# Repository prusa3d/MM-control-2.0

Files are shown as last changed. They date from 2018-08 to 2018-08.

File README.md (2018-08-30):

# PRUSA MM control board

KiCad PCB layout
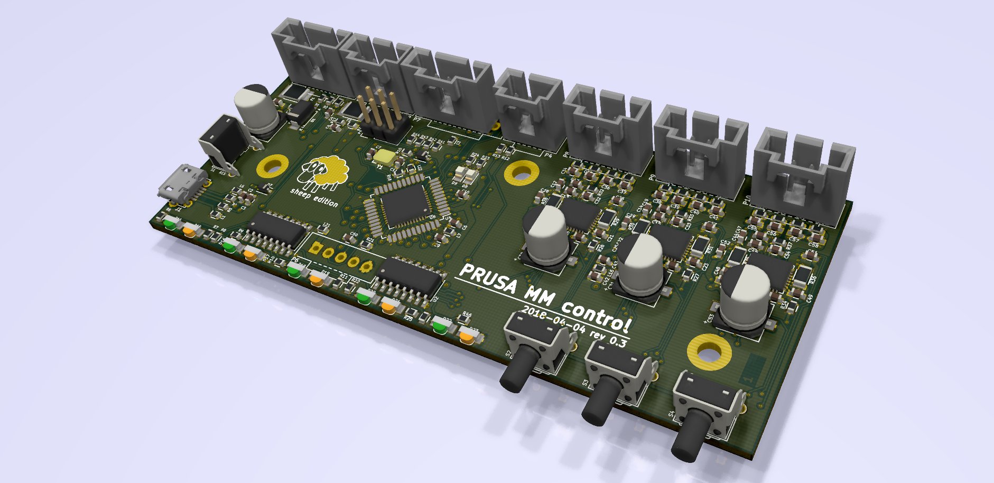
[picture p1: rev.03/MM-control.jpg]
PCB


* [Interactive bom](http://htmlpreview.github.io/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)
* [STEP 3D model](rev.03/MM-control.step)
* [Firmware](https://github.com/prusa3d/MM-control-01)

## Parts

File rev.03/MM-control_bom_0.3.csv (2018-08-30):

Component | Description | Part | References | Value | Footprint | Quantity Per PCB | Req
1 | Unpolarized capacitor | C | C1 C2 C4 C9 C12 C14 C16 C17 C18 C19 C20 C21 C22 C23 C24 C25 C26 C27 C28 C29 C42 C44 C46 C47 C48 C49 C50 C51 C52 C60 | 100n | C_0603 | 30 | 50V/X7R/10%
2 |  | Csmall | C8 | 100n | C_0603 | 1 | 50V/X7R/10%
3 | Polarised capacitor | CP_Small | C30 C31 C53 C59 | 100u | c_elec_6.3x7.7 | 4 | 35V/20%
4 | Unpolarized capacitor | C | C3 | 10u | C_0603 | 1 | 6,3V/X5R/20%
5 | Polarised capacitor | CP_Small | C43 | 10u | C_0603 | 1 | 6,3V/X5R/20%
6 | Unpolarized capacitor | C_Small | C34 C35 C36 C37 C38 C39 C40 C41 C55 C56 C57 C58 | 1n | C_0603 | 12 | 50V/X7R/10%
7 | Unpolarized capacitor | C | C6 C10 C32 C33 C54 | 1u | C_0603 | 5 | 6,3V/X5R/10%
8 | Unpolarized capacitor | C_Small | C13 C15 C45 | 22n | C_0603 | 3 | 50V/X7R/10%
9 |  | Csmall | C7 C11 | 22p | C_0603 | 2 | 50V/C0G/10%
10 | Diode, alternativ symbol | D_ALT | D6 D7 | BAS16HT1G | SOD-323 | 2
11 | LED, small symbol, alternativ symbol | LED_Small_ALT | D14 D16 D18 D20 D22 | KPA-3010MGC | LED-1104 | 5
12 | LED, small symbol, alternativ symbol | LED_Small_ALT | D15 D17 D19 D21 D23 | KPA-3010SECK | LED-1104 | 5
13 | LED generic, alternativ symbol | LED_ALT | D8 | RX | LED_0805 | 1
14 | Diode, alternativ symbol | D_ALT | D1 | SK310SMA-DIO | SMA_Standard | 1
15 | LED generic, alternativ symbol | LED_ALT | D9 | TX | LED_0805 | 1
16 | resettable fuse, polymeric positive temperature coefficient (PPTC), small symbol | Polyfuse_Small | F1 | 150mA | R_1812 | 1
17 | resettable fuse, polymeric positive temperature coefficient (PPTC), small symbol | Polyfuse_Small | F2 | 750mA | R_1812 | 1
18 |  | USB-micro | J1 | MX-105017-0001 | USB-micro | 1
19 | Inductor with ferrite core, small symbol | L_Core_Ferrite_Small | L1 L2 L3 L5 L6 L7 L8 L9 L10 L11 L12 L13 L14 L15 L16 L17 L18 L19 L20 L21 L22 | FB BLM18KG121TN1D | R_0603 | 21
20 |  | CONN_3X2 | P5 | ICSP | Pin_Header_Straight_2x03 | 1
21 | Connector, single row, 01x03 | CONN_01X03 | P4 | MOLEX 70543-0002 | Pin_1x03-XL | 1
22 | Connector, single row, 01x04 | CONN_01X04 | P8 P9 P10 | MOLEX 70543-0003 | Pin_1x04-XL | 3
23 | Connector, double row, 02x02 | CONN_02X02 | P2 | MOLEX 70543-0003 | Pin_1x04-XL | 1
24 | Connector, single row, 01x06 | CONN_01X06 | P7 | MOLEX 70543-0004 | Pin_1x06-XL | 1
25 | Connector, single row, 01x05 | CONN_01X05 | P1 | MOLEX 70543-0004 | Pin_1x05-XL | 1
26 | Connector, single row, 01x05 | CONN_01X05 | P6 | ShiftOut | Pin_1x05-XL | 1
27 | Resistor | R | R41 R42 R43 R44 | 0R | R_0603 | 4 | 0,1W/5%
28 | Resistor | R | R12 | 100R | R_0603 | 1 | 0,1W/1%
29 | Resistor | R | R32 R33 R37 | 10R | R_0603 | 3 | 0,1W/1%
30 | Resistor | R | R13 R15 R16 R21 R26 R27 R34 | 10k | R_0603 | 7 | 0,1W/1%
31 | Resistor | R | R38 | 15k | R_0603 | 1 | 0,1W/1%
32 | Resistor | R | R18 | 1M | R_0603 | 1 | 0,1W/1%
33 | Resistor | R | R17 R23 R24 | 1k | R_0603 | 3 | 0,1W/1%
34 | Resistor | R | R39 R40 | 1k5 | R_0603 | 2 | 0,1W/1%
35 | Resistor | R | R1 R2 R4 R5 | 22R | R_0603 | 4 | 0,1W/1%
36 | Resistor | R | R6 R7 R8 R9 R10 R11 R22 R25 R45 R46 | 330R | R_0603 | 10 | 0,1W/1%
37 | Resistor | R | R28 R29 R30 R31 R35 R36 | R22 | R_1206 | 6 | 0,5W/1%
38 |  | TACT-SW2 | S4 | DWN | TACT-90 | 1
39 |  | TACT-SW2 | S2 | OK | TACT-90 | 1
40 |  | TACT-SW2 | S1 | RES | TACT-90 | 1
41 |  | TACT-SW2 | S3 | UP | TACT-90 | 1
42 |  | 74HC595 | U2 U9 | 74HC595 | SOIC-16_3.9x9.9mm_Pitch1.27mm | 2
43 |  | ATmega32U4 | U4 | ATmega32U4 | TQFP-44_10x10mm_Pitch0.8mm | 1
44 |  | ATmega32U4 | U8 | ATmega32U4 | QFN-44-1EP_7x7mm_Pitch0.5mm | 1
45 |  | TCM2130-LA | U5 U6 U7 | TMC2130-LA | QFN-36-1EP_5x6mm_Pitch0.5mm-GNDpad-0.3mm | 3
46 | Four pin crystal (GND on pins 2 and 4), e.g. in SMD package | Crystal_GND24 | Y1 | LFXTAL035264BULK 16MHz | Crystal-3.2x2.5mm | 1
Component Groups: | 46
Component Count: | 161
Fitted Components: | 161
Number of PCBs: | 1
Total components: | 161
Schematic Version: | 0.3

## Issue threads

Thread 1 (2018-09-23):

kiCAD files do not reflect actual MMU2 production board.

CacikeOtoao, 2018-09-23:
@ok1hra Production boards of the MMU2 that people are getting are showing re work to the vias (to the upper right of the sheep logo) after manufacturing that are not reflected on the Source files provided here. Keep in mind that these files were made public after the MMU2 was released and corrections as described above had been made to the boards. Please provide updated documentation or comments regarding these changes as good Open Source practice. Providing outdated information to the community is not a good practice since the community depends on these files to replicate the boards and Prusa Research preaches about Open Source.

ericclinedinst, 2018-09-23:
My level of surprise is absolutely zero.

ok1hra, 2018-09-23:
@CacikeOtoao thanks for comment. Can you show me this difference? Because revision 0.3 is last production version

ericclinedinst, 2018-09-23:
@ok1hra  for starters R42, d7, r44 are removed on the boards you're shipping.   Where as the BOM has them in place.

ericclinedinst, 2018-09-23:
In some photos it appears that traces have been cut above the sheep on the right side just above his butt.

Also when will we be getting the bootloader that was spoken about in anot her github thead? You guys said a week ago it would be posted in "days" @ok1hra

ok1hra, 2018-09-23:
And you can post this photos? Without another argument you claim is false.

I am not manage bootloader, I cant help you. Ask on support desk.

Closed 2018-09-23.

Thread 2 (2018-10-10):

The orentation of the sockets should be turned by 180°

KarlZeilhofer, 2018-10-10:
Is there any chance, that the sockets will be turned by 180°?
With the current case of the MMU 2.0 is nearly impossible to unplug the cables when everything is assembled.

ok1hra, 2018-10-11:
We do not have the same feeling.

KarlZeilhofer, 2018-10-18:
No, why not? I think to remember, that the trouble shooting guide says to use an allen key to unlock the securing pin of the communication plug.

domesticatedviking, 2019-09-16:
I very much agree.  When using an enclosure, all of the connections to the MMU2 are in a location that can neither be seen nor reached from the front of the printer, and they all require tools to remove.   The result is that it is VERY difficult to remove the printer for maintenance.   This is why I designed the [underslung control panel mod](https://www.thingiverse.com/thing:3211711).

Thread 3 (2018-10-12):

100nF for VCC of MCU

KarlZeilhofer, 2018-10-12:
I would suggest 100nF ceramic capacitor for pins 2, 14 and 34, since they are all powered via ferrite beads, just to be on the save side.

ok1hra, 2018-10-17:
Yes, good idea for next version. Thanks.

pacaj2am, 2021-02-14:
wow... having issues with my board... looking into the design... haven't expected such a design flaws (as well as the C60 issue
https://github.com/prusa3d/MM-control-2.0/issues/12)

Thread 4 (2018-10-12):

Signal directions of global labels should be corrected

KarlZeilhofer, 2018-10-12:
Many labels are pointing into the wrong directions.

This is more a matter of taste: Since KiCad has no ability to automatically show where global labels are referenced, I would prefer wires instead of excessive usage of labels, where easily possible:
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

ok1hra, 2018-10-17:
Does not affect to functionality :)

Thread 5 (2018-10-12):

ERC Errors should be cleaned up

KarlZeilhofer, 2018-10-12:
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

The use of the power-flag should fix many of them. We at Team14 also use passives with a dedicated direction, to give the ERC more chances to detect errors.
Once I wrote an article about that: http://www.zeilhofer.co.at/wiki/doku.php?id=resistors_and_void-pointers

Many of them would need to modify the MCU symbol pins to outputs, which isn't very handy either. That's a common problem. Perhaps one could introduce a special symbol, similar to a power-flag, which declares a driver to that net (virtual symbol with a single "output" pin).

ok1hra, 2018-10-17:
Nice tutorial, thanks.

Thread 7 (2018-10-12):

TODO: button expansion connector

KarlZeilhofer, 2018-10-12:
just a duplicate of a note in the schematic :)

ok1hra, 2018-10-17:
also in plan

Wheart, 2021-11-27:
Is it implemented on 0.4.4?

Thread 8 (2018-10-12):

Missing comments about number of axis and LEDs

KarlZeilhofer, 2018-10-12:
I know, this is defined in software, but it helps, if it is clearly visible in the schematics too.

ok1hra, 2018-10-17:
yes, but is not exact :)

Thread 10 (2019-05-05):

noise in idle, homing problems, led flickering

SNDR0, 2019-05-05:
like said from @chriswal, adding  a ceramic capacitor 104 between pin 16 and ground of every 74hc595 you solve the problem. (issue known when you are using 74hc595)

darBis, 2019-06-13:
I had recently solved these issues by adding 100 nF capacitors to 74hc595 ICs also.(https://github.com/prusa3d/MM-control-01/issues/124#issuecomment-501355623)
Please add bypass capacitors to those ICs in next revision of the board.
Information about this issue and working solution is relatively hard to find, maybe some list of known issues on wiki would be great.

darBis, 2019-08-24:
This is a serious reliability issue. Since fixing my board by adding those caps i have no more issues with the MMU regarding homing errors and erratic behaviour.

chriswal, 2019-08-24:
i also made a firmware workaround for people who cant modify the board on there own. there is a pull request. or you can get it from my fork

bbeller123, 2020-07-30:
Prusa should add a screen with graphic interface for multi material. I mean it's multi color ?

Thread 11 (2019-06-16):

mmu2 stepper are always powered up

sylphio, 2019-06-16:
hi,
   my prusa mk3 use octoprint on a internal raspberry, so i leave the printer always on.
Just realised that after 2 day of idling the mmu2 steeper are still hot and powered. (the printer steeper are cold)
It is not great for power consumtion and for long term usage.

Is it possible to powerdown after a certain time of inactivity?

Thank you

sylphio, 2019-06-16:
Just realized this one is for the hardware and not the sorftware

Closed 2019-06-16.

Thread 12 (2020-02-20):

C60 can cause timing issues

NielschB, 2020-02-20:
I have experienced some issues with my MMU2 board, where all LEDs started flashing and could not get the motors working anymore. All pinned down to capacitor C60 which is connected to the latch input of the shift registers. This caused a slow ramp of the latch signal which resulted in timing issues on the shiftregister side. After reviewing the schematics I wonder why C60 is there in the first place. If its function is to implement a low-pass filter, then a series resistor should be added, now its determined by the Atmega output drive strength.
All together this is not a nice way to do this since a slow signal ramp is applied to a digital input (cross currents etc.) Another thing is that continuously charging and discharging this cap by the MCU is a waste of current.

chriswal, 2020-07-30:
and you resolved this issue by removing C60?

NielschB, 2020-07-30:
Yes, just remove it

NielschB, 2020-07-30:
This C60 might just be there to give non-prusa sellers a hard time ;) I have the feeling that the original Prusa boards might not have this cap assembled.

chriswal, 2020-07-30:
You are right , there should be a resistor in series. but i dont see where there is a timining issue. the enable signals are always on, only the dir signals can change because of the direction the motor is moving. the leds are working also without a problem.
so what is the timing issue you are refering about?

NielschB, 2020-07-30:
Most boards don't show the issue, I have had 2 boards that did have this timing issue. Most probably its related to the output drive strength of the MCU where the cap is connect to, which determines the slope of the latch signal. It might vary over batches. Again, in the end a design should never have an analog LPF on a digital input like this.

When the MCU is shifting out data to the shift registers, the latch signal should toggle at a certain moment in time to load the data in the registers. When the latch signal is being delayed (By the cap and finite drive strength of MCU) the latch signal is crossing the shift register's threshold when next data is already shifted in! which causes corruption of the data in the shift registers.

chriswal, 2020-07-30:
So you had flickering leds and loud motor noises on this boards?

NielschB, 2020-07-30:
Flickering leds yes, motors would just not turn in my case, but I expect anything can hapen.
May I ask why you are interested? Are you experiencing the same issues?

chriswal, 2020-07-30:
i edited the message before.  yes i had this issue and solved it a different way.

chriswal, 2020-07-30:
if the motor doesnt turn then this could be some different problem than mine

NielschB, 2020-07-30:
I did try the buffer capacitors, did not help for me. Then I traced it down to this issue which was confirmed with scope measurements.
I am wondering if the people who fix their issue with adding decoupling caps to the shift registers are actually suffering this C60 issue and the error is masked with adding buffer caps. Charging / discharging C60 takes quite some current which could explain why adding buffer caps could help.

Shift registers producing random data due to lack of decoupling caps would mean that the supply drops significantly, which I personally have not observed. (I did measure it actually)

chriswal, 2020-07-30:
but that is a small capacitor and it is charged from the mcu... so for the layout that is further away from the register.
i think to measure this you have to have a very fast scope. is it possible that on these board you had wrong capacitors assembled?
i caan repoduce it on my board if i remove the buffer capacitors.. i also made a workaround in the firmware where you dont change leds while moving the motor ..
i can try to remove the capacitor..i think they added it because they had problems before with erratic output

chriswal, 2020-07-30:
i didnt build this system ..i had this board ..and some of the people are not able to solder.. so i made this workaround ..
i can solder so i can fix something..i have a 100mhz scope but not around at the moment. and this was not an assumption
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
from the datashhet

chriswal, 2020-07-30:
but there can be multiple problems leading to the same outcome. thats why i am interested to find the real problem.
there is also a problem with the design of the 5v power on this board.

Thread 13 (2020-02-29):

Cables

ThomasLGauthier, 2020-02-29:
Hello everyone,

I'd like to implement https://www.prusaprinters.org/prints/7499-prusa-mmu2-moving-filament-passage-22mm-ikea-plats, but the cables between the MMU2S and the MK3S are too short. What cables do I need to buy in a longer form to do what I want? What are the names/links to them? I am also planning to move the power unit outside the enclosure, so what cables might I need to get for that?

Sincerely,
Thomas Gauthier

covertpluto3502, 2022-12-29:
They're molex SL connectors, more specifically the 2.54mm pitch single row versions

Grab some long dupont breadboard jumper wires and take the plastic housings off.

Buy these:(4 pin male, 4 pin female, 5 pin male, 5 pin female)

https://uk.rs-online.com/web/p/wire-housings-plugs/6795971
https://uk.rs-online.com/web/p/wire-housings-plugs/9081005

https://uk.rs-online.com/web/p/wire-housings-plugs/6783161
https://uk.rs-online.com/web/p/wire-housings-plugs/6795921

Then just jam the metal ends of the dupont wires into the housings so the pins on both ends match up. The female ends on the dupont wires(the one with a hole on its end) goes into the female housing and vice versa

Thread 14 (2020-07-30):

Feature Request: Add LCD and Pass Selftest for Multi-Material Upgrade

bbeller123, 2020-07-30:
Prusa should add a screen for the multi material. It would help solve and/or explain problems through graphic text to the user. Something with the color display like the Prusa Mini?

With the screen, there could be a pass selftest feature similar to the current MK3S.

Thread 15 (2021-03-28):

Design error on +5V net

HenrikBork, 2021-03-28:
Hi,
There seems to be a bug in the design regarding the +5V net.
On my MMU2 i measured 4.2V on the +5V, which is too little for the MCU to run 16MHz. This is seemed to be the reason why my MMU was almost unusable as the MCU resets all the time.
Connecting the usb to a host helped a little on stabillity (and the +5V voltage rose 50-100mV)
I have shorted D1 on the MMU PCB, as a "proof-of-problem", and that raised the voltage to 4.8V and removed all MMU misbehavings. (without the usb connected). In the same bug chasing i also added 1000uF between the shorted D1 and GND. I think C59 was probably just fine as it is. (i was tiered of bug chasing the MMU)
**Please note: this is not a proposal to a solution, just "proof" of some kind of an issue with the +5V (at least on my MMU). I have no understanding of the diode's function in the entire printers power nets.** -although this hack has been working for some time now.

So it seems as if the designer was aiming for generating +5V by means of the TMC2130. But forgot to connect the VSA to >6V. But then again why differ so much from the suggested circuit and component values?...
The solution of using the printers +5V through a diode and a inductor yields too low a voltage.
...so it seems as the +5V was forgotten, but it somehow sometimes almost works...

My hope is that Prusa fix this problem in the hardware design. (and sends me a fixed PCB free of charge ;-)

### You're welcome,
### Henrik B. S.

My setup:
Original Prusa I3MK3 (2-3 years old), since then upgraded with factory parts.
MMU2 bought from Prusa around august 2020.
MMU PCB reads "2019-09 rev 0.4.4"
My ugly hack:
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

extra info:
I also reported/discussed this on [https://forum.prusaprinters.org/forum/original-prusa-i3-mmu2s-mmu2-hardware-firmware-and-software-help/i-found-serious-design-error-in-mmu2-electronics-hardware/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](https://forum.prusaprinters.org/forum/original-prusa-i3-mmu2s-mmu2-hardware-firmware-and-software-help/i-found-serious-design-error-in-mmu2-electronics-hardware/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)
...My daytime job is to do this kind of work as consultant - so next time just hire me :-)

Chrismettal, 2021-05-22:
Can confirm, my board started to reset every time it needed to unload filament, getting stuck and requiring user input on every single filament change.
Bypassing the diode raised the 5 V rail from 4.6 V to 4.95 V in idle, fixing the resetting issue for now. Before I could see dips under 4.5 V on the rail on filament changes at which point the MCU sometimes reset.

The capacitor does not seem to be required for me, but I have also added the missing decoupling caps on the shift registers.

Thank you for your find and I sincerely hope Prusa did not abandon the MMU2 and are going to release a new Version of the board (Or maybe at least publish the sources of the most recent version since this repo is behind the actually released boards)

ANTALIFE, 2022-01-03:
Good catch! Looks like quite a big HW bug...
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

ChrisPetit, 2022-06-20:
it has been a year...is this being addressed? I haven't had a correct functioning MMU2S since it was first released...

Kugelfang666, 2022-06-20:
Same problem with me, adding a 5V USB PSU to the MMU reduced the frequency of this problem coming up but it still happens every now and then

lemmingDev, 2022-08-27:
So, is there a verified fix for this hardware issue yet?

Kugelfang666, 2022-08-27:
Yep, adding a stepsons to provide the 5V line of the 12 line permanently fixed the issue for me. Check out the tread in the Prusa Forum. All the details are there an I can verify that this is working. Did a multicolor print yesterday and not a single problem!

vladimir-aubrecht, 2022-09-07:
@ok1hra Do you think you could help with some official statement on this issue?

I think any answer would be better than none as it's keeping people in a void of not knowing if it make sense to wait for some kind of official fix (or even new version of the board) or they should just try to fix it themselves/sell mmu2s/...

Unfortunately I started to hit this issue too 😕

JakoobCZ, 2022-10-04:
Hi,
sorry for the late response. We are working on updates to the MMU2S. Our devs are finalizing new smarter firmware, which will bring new features along with improved performance and reliability to the MMU2S - all on the current motherboard. The new firmware is being tested on multiple printers and so far the results look very promising - we're focusing on the elimination of restarts caused by low voltage, reducing required user interventions and overall better user experience. I can't promise any ETA, but we are doing our best to have it done as soon as possible.

Chrismettal, 2022-10-05:
This is great news and I am extremely grateful for an update. Thank you!
A little communication goes a long way, and sharing any progress helps users keep faith in the project.

Can you share the reason why development isn't done in a publically visible branch? Even having the actually released board revision visible here would be an upgrade, as the repo seems to be lagging behind the actually available product version.

GRIFFCOMMca, 2023-06-03:
I have arrived here as the 2019 MK3s with the MMU2s seems to have the same issue, many resets, this only really started to happen recently, we have not modified the printer, we have a Pi Zero, which was upgraded to a Pi Zero 2 in the past 4 months, we found it abit better when moving the data cables for the front LCD away from the data cable from the MMU2s, still has MANY issues with constant resets resulting in 5 green / orange flashing LEDs,

How is the firmware coming as this is really now unusable.

dtryba, 2023-07-30:
> How is the firmware coming as this is really now unusable.

The new firmware is out and the results is that it worsened this bug.

I had this issue when I installed a switch to the MMU2S to easily disable it, so remove the switch again.
The MMU2S worked fairly well with older stock, it worked fine with The Zero Beast firmware. With 3.0.13 and MMU3_3.0.0+814.hex the MMU2S became unworkable. Power issues resulting in "MMU MCU ERROR 04306" and ""MMU SELFTEST FAILED 04325", followed by "IDLER CANNOT HOME 04125" when it got past the first 2.

Shorting the diode didn't resolve these issues. So that finally drove me to install a DC-DC boost converter between the printer and pin 1. Ramping up the voltage after the diode to 4.9V appears to have given me a workable MMU2S again.

Version of MMU board: 0.3 producion date 2018-04-2x.

JanMrlth, 2023-08-05:
I updated the MK3s+ to 3.13.0-6873 and the MMU2S to 3.0.0 with the result, that I get a 'MMU MCU ERROR 04306' all the time.

puckpuck, 2023-09-09:
I suspect a power problem with my MMU2S after over 2 years of hassle-free usage. Waiting for the new firmware, I finally had time to try it out, and upon first boot, I get the 04306 error.

So, this feels like a hardware issue now. Is Prusa able to help here? Is my only option to buy another MMU mainboard and wait for it to ultimately fail on me again?

SixOThree, 2023-09-29:
Before finding information suggesting a design issue I replaced that MMU mainboard (at my own expense). Then I replaced all of the stepper motors, one by one, again at my own expense. I worked with tech support and posted on and created multiple threads with no suggestion there is a mainboard design issue. Not particularly please with what I am seeing.
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
lemmingDev, 2023-12-12:
Lucky AliExpress has you covered ;)
https://www.aliexpress.com/item/1005006221728533.html

phat3r, 2023-12-12:
$40 for part that isn't needed - value ... Just 5 minutes work to de-pin and move the blue wire over to the SPI as per Chris Riley suggestion above ... I have done it on both my MMU2's ... one a clone and one original prusa and has resolved all the power / logic nonsense.   If you want to make it super near ... use a 2c dupont connector - the pin will go into it.

lemmingDev, 2023-12-12:
Yeah - I personally used buck converters for my 3 when it was orinally suggested, though if I were to do it again, I would do as above, and not spend any money...

eoyilmaz, 2023-12-28:
> It works. Now the firmware is not raising the error about the lack of voltage.
>
> ![image](https://private-user-images.githubusercontent.com/7290345/280298602-94d2f685-4dbb-408a-8f7b-58ee198f7787.png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)

Hey, isn't this the 10 color version :)

roster210, 2024-04-05:
This is outrageous we all had faith with them as a company and they have known about this issue and not addressed it for years and the fact the fix is so easy is out of this world, Josef Prusa obviously only cares about more money, they have enough resources to cover this issue, the profit margins on this non working device are out of this world and they still push the issue so  far and do not address it or release a fix until after most peoples or all peoples warrantys are void. I own two and have for years and they are decent printers but that is not a decent company, they have multiple firmware versions that have fried boards then dont honor that fix unless you are in your 1 year warranty range and then they have this.  they have their propritary einsy rambo that is just a pain to  deal with compared to ulti's or even any knock off chinese ones. in hindsight it feels obvious they only care about themselves and Josef, mostly josef and it feels obvious because of the multiple pictures of his arrogant face and the namesake the company. I am not surprised that they evade the issue by ignoring knowledge of it, they seem to b e better at it then the chinese manufactured ones- who have replaced components just off proof of sales, its outrageous this overpriced machine does not give the support you would assume you should get for a $1100 setup at the time. We spend 1000 and prusa cant give us something that costs them <$5 to be able to use our machine. I am going to make as much noise as i canabout this online, its outrageous that this is all it needed and they held onto it until mmu3... on the positive side- i now know a lot more about printers because of fixing and trying to fix this and other issues. Ill never buy a prusa from prusa again and ill  never buy one unless its 1/4 of their price, ill never give that man or his company money again they do not deserve it.

lemmingDev, 2024-04-06:
Yeah - I feel your pain
For my school, I suggested we buy 7 x MK3S and 3 x MMU2S a number of years ago
We were never able to get the MMU2S working at all and just removed them

Over the years I tried many different 3D parts from DIYers to fix the issues, but it hasn't been until recently when the DIY power fix was worked out that they've now been able to be actually used semi-reliably

I'm in charge of purchasing and we won't be buying Prusa when they're due to be replaced do to this fiasco

The MK3S machines we bought have been fairly reliable and I've been able to maintain them
A Y stepper on an Einsy died a year ago and I replaced it with a clone Einsy off AliExpress
An MMU board died too, and I replaced it with one off AliExpress too
A few heater cartridges, thermisters and fans have also had to be replaced

Closed 2024-05-07.

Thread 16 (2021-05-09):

Schematic for rev 0.4 and later?

Redferne, 2021-05-09:
Have connected a I2C display to the P7 port, but need an additional IO pin. Problem is that rev 0.3 schematic shows that P7 is a 6 pin connector, but in rev 0.4 and later it is in reality a 5 pin connector. What is connected to pin 5? Is it SCK, D7 or some other pin?

ok1hra, 2021-05-10:
P7 is 6 pin hole in PCB, but soldered only 5 pin connector. P7.6 not used.

Closed 2021-05-10.

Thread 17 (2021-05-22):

Motor Sync

gdville, 2021-05-22:
I have an issue, out of the box after installing MMU2s on already functioning MK3S+. 

Problem 1: First of all, idler does not align properly for feeding filament 1.  The selector aligns correcty, and pulley turns in correct direction for loading filament. After manually repositioning idler, filament 1 will load to nozzle.

Problem 2: It appears that firmware does not sync the MMU pulley motor to the extruder motor. 

     2a. They turn at different speeds during load to nozzle.

     2b. During 1st layer calibration they do not turn at the same time and sometimes even turn in opposite directions, leading to filament grinding and missed steps. 

Is this lack of synchronization a "feature" I'm not understanding, a common bug, or an indicator of some other issue?

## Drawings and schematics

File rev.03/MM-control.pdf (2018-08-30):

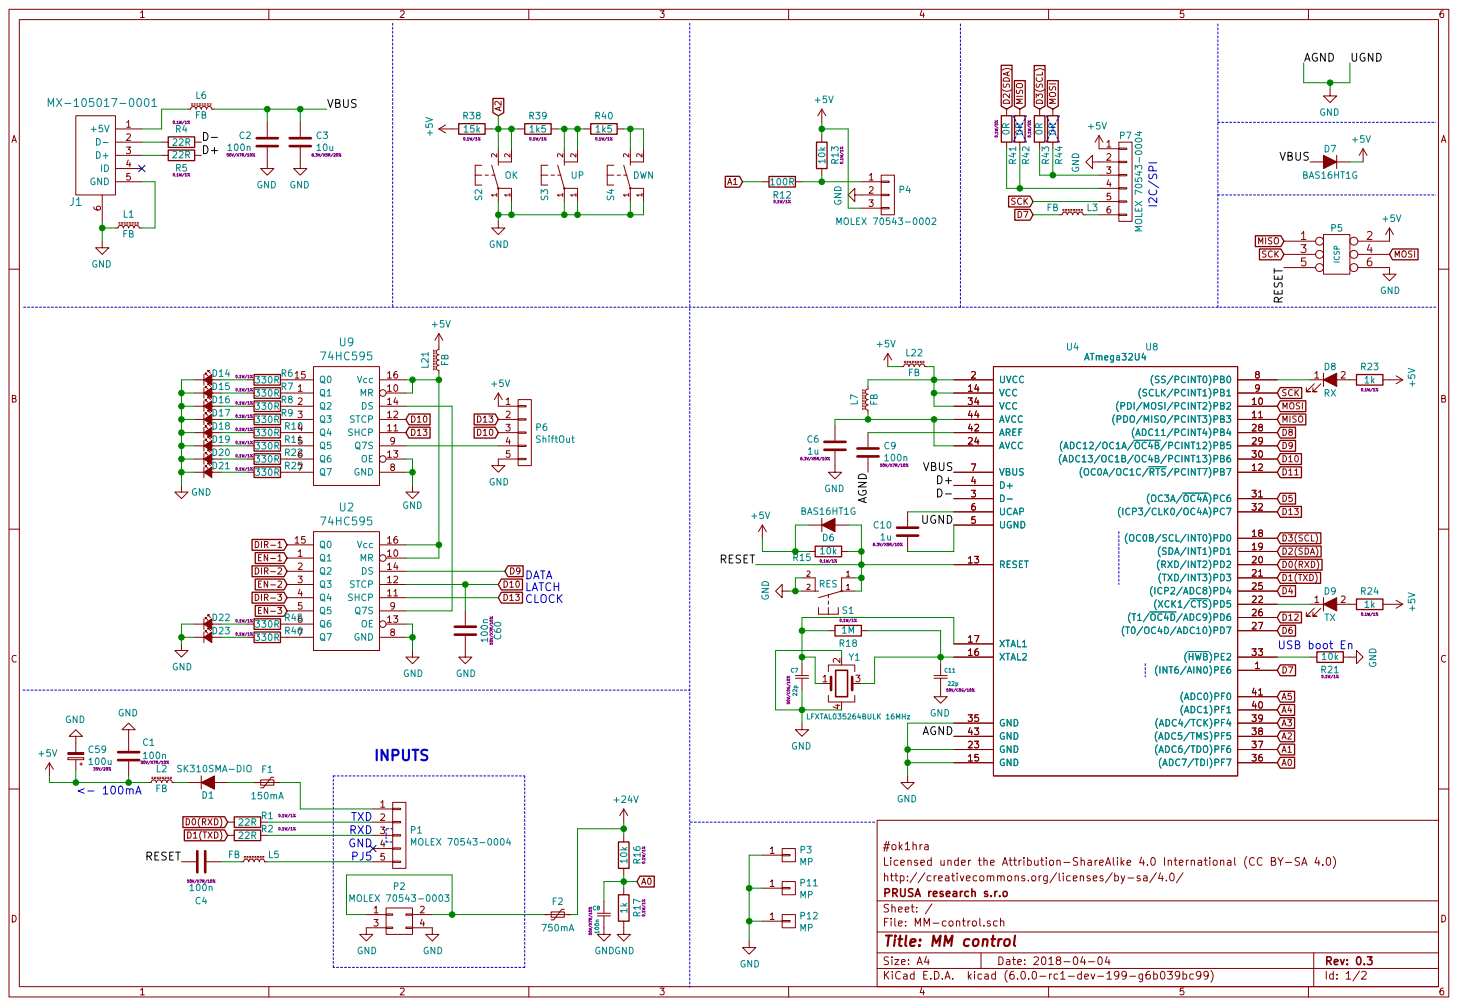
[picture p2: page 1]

Licensed under the Attribution-ShareAlike 4.0 International (CC BY-SA 4.0) #ok1hra

http://creativecommons.org/licenses/by-sa/4.0/
Id: 1/2 Title: MM control File: MM-control.sch Sheet: / PRUSA research s.r.o

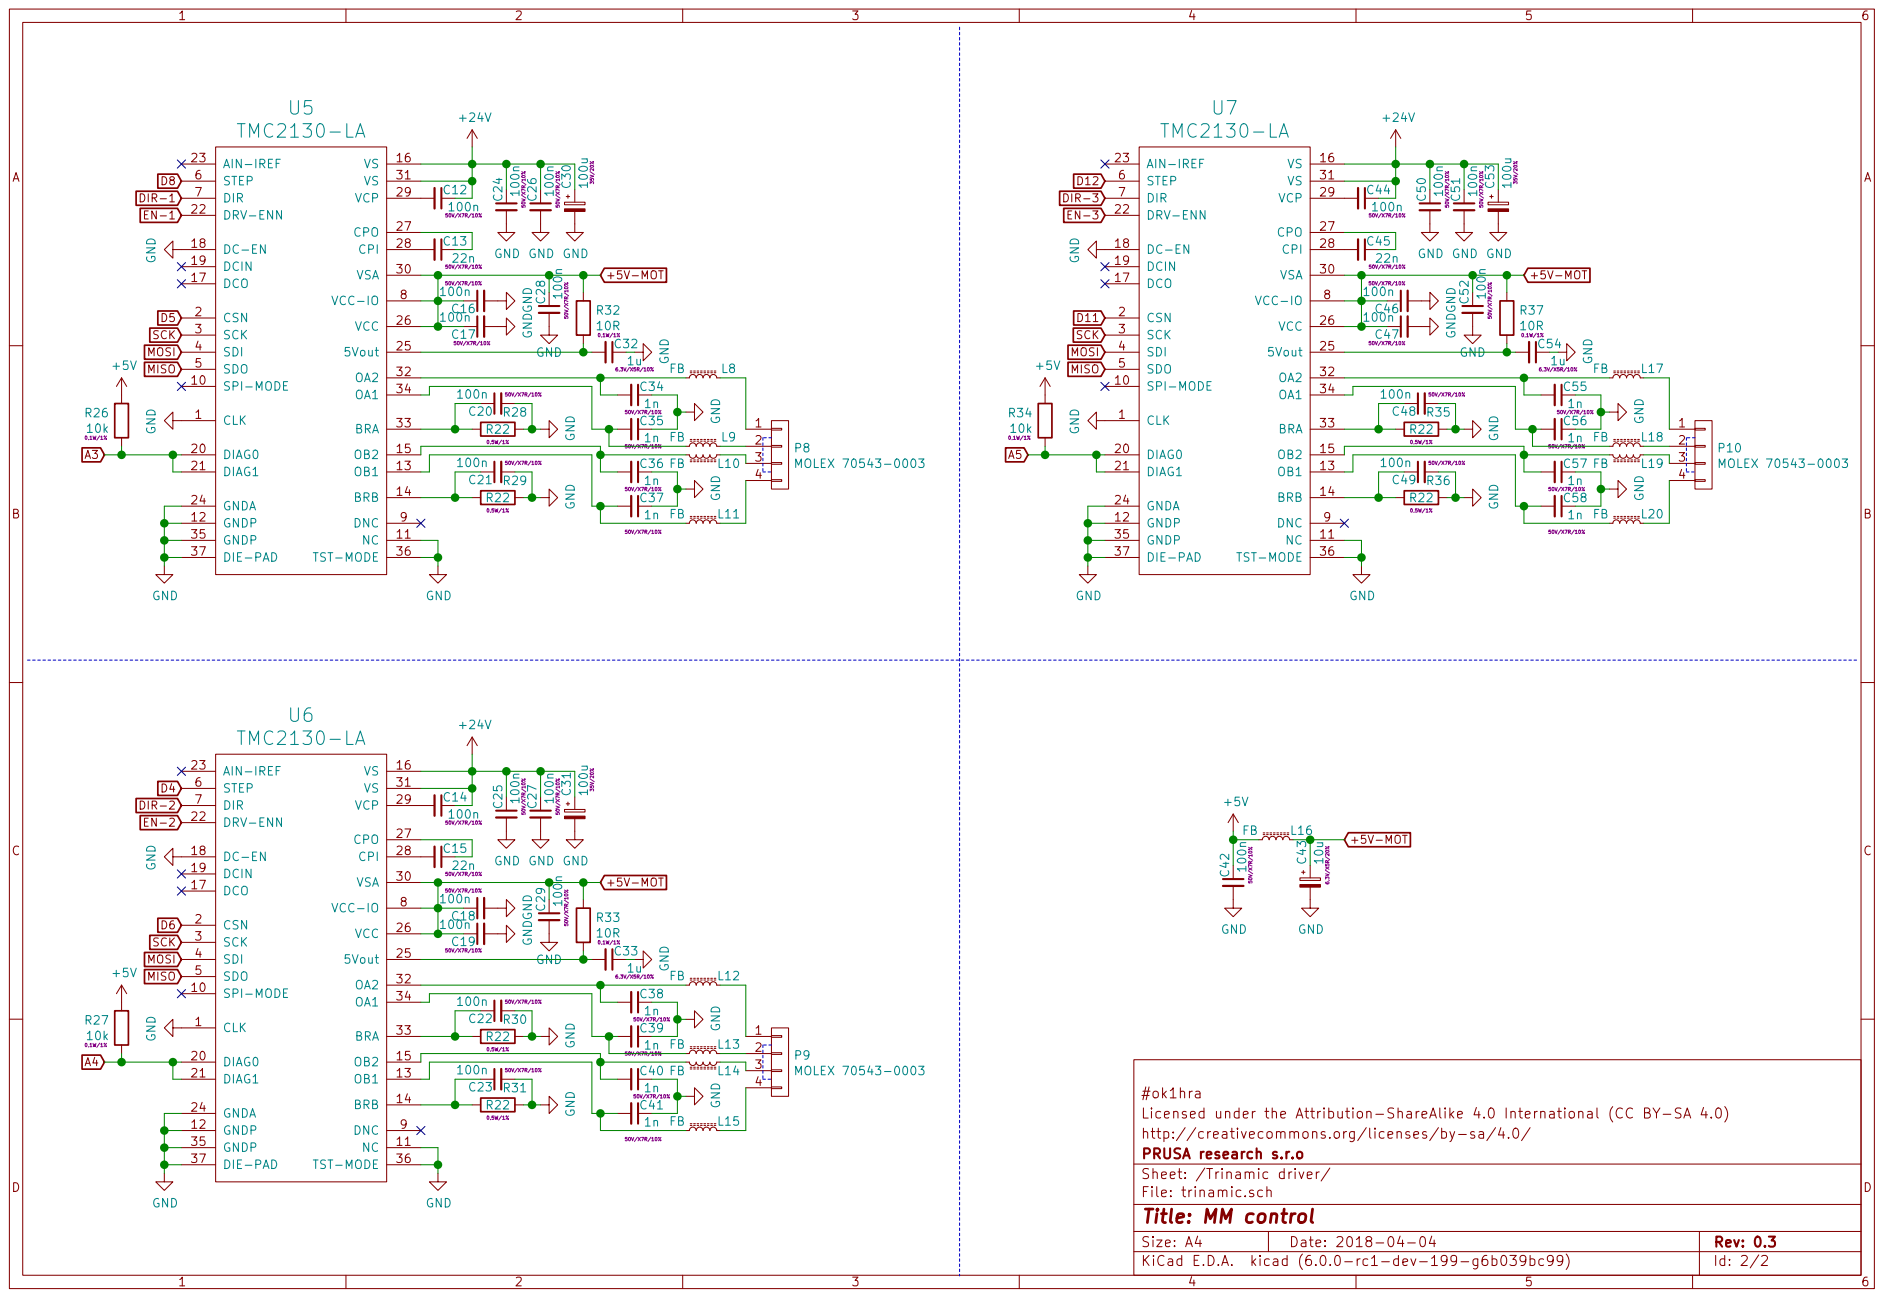
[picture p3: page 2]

TMC2130-LA GND SCK MOSI MISO GND

DIR-1 D5 GND SCK MOSI MISO GND

EN-2 GND SCK MOSI MISO GND

Licensed under the Attribution-ShareAlike 4.0 International (CC BY-SA 4.0) #ok1hra

http://creativecommons.org/licenses/by-sa/4.0/
Id: 2/2 Title: MM control File: trinamic.sch Sheet: /Trinamic driver/ PRUSA research s.r.o

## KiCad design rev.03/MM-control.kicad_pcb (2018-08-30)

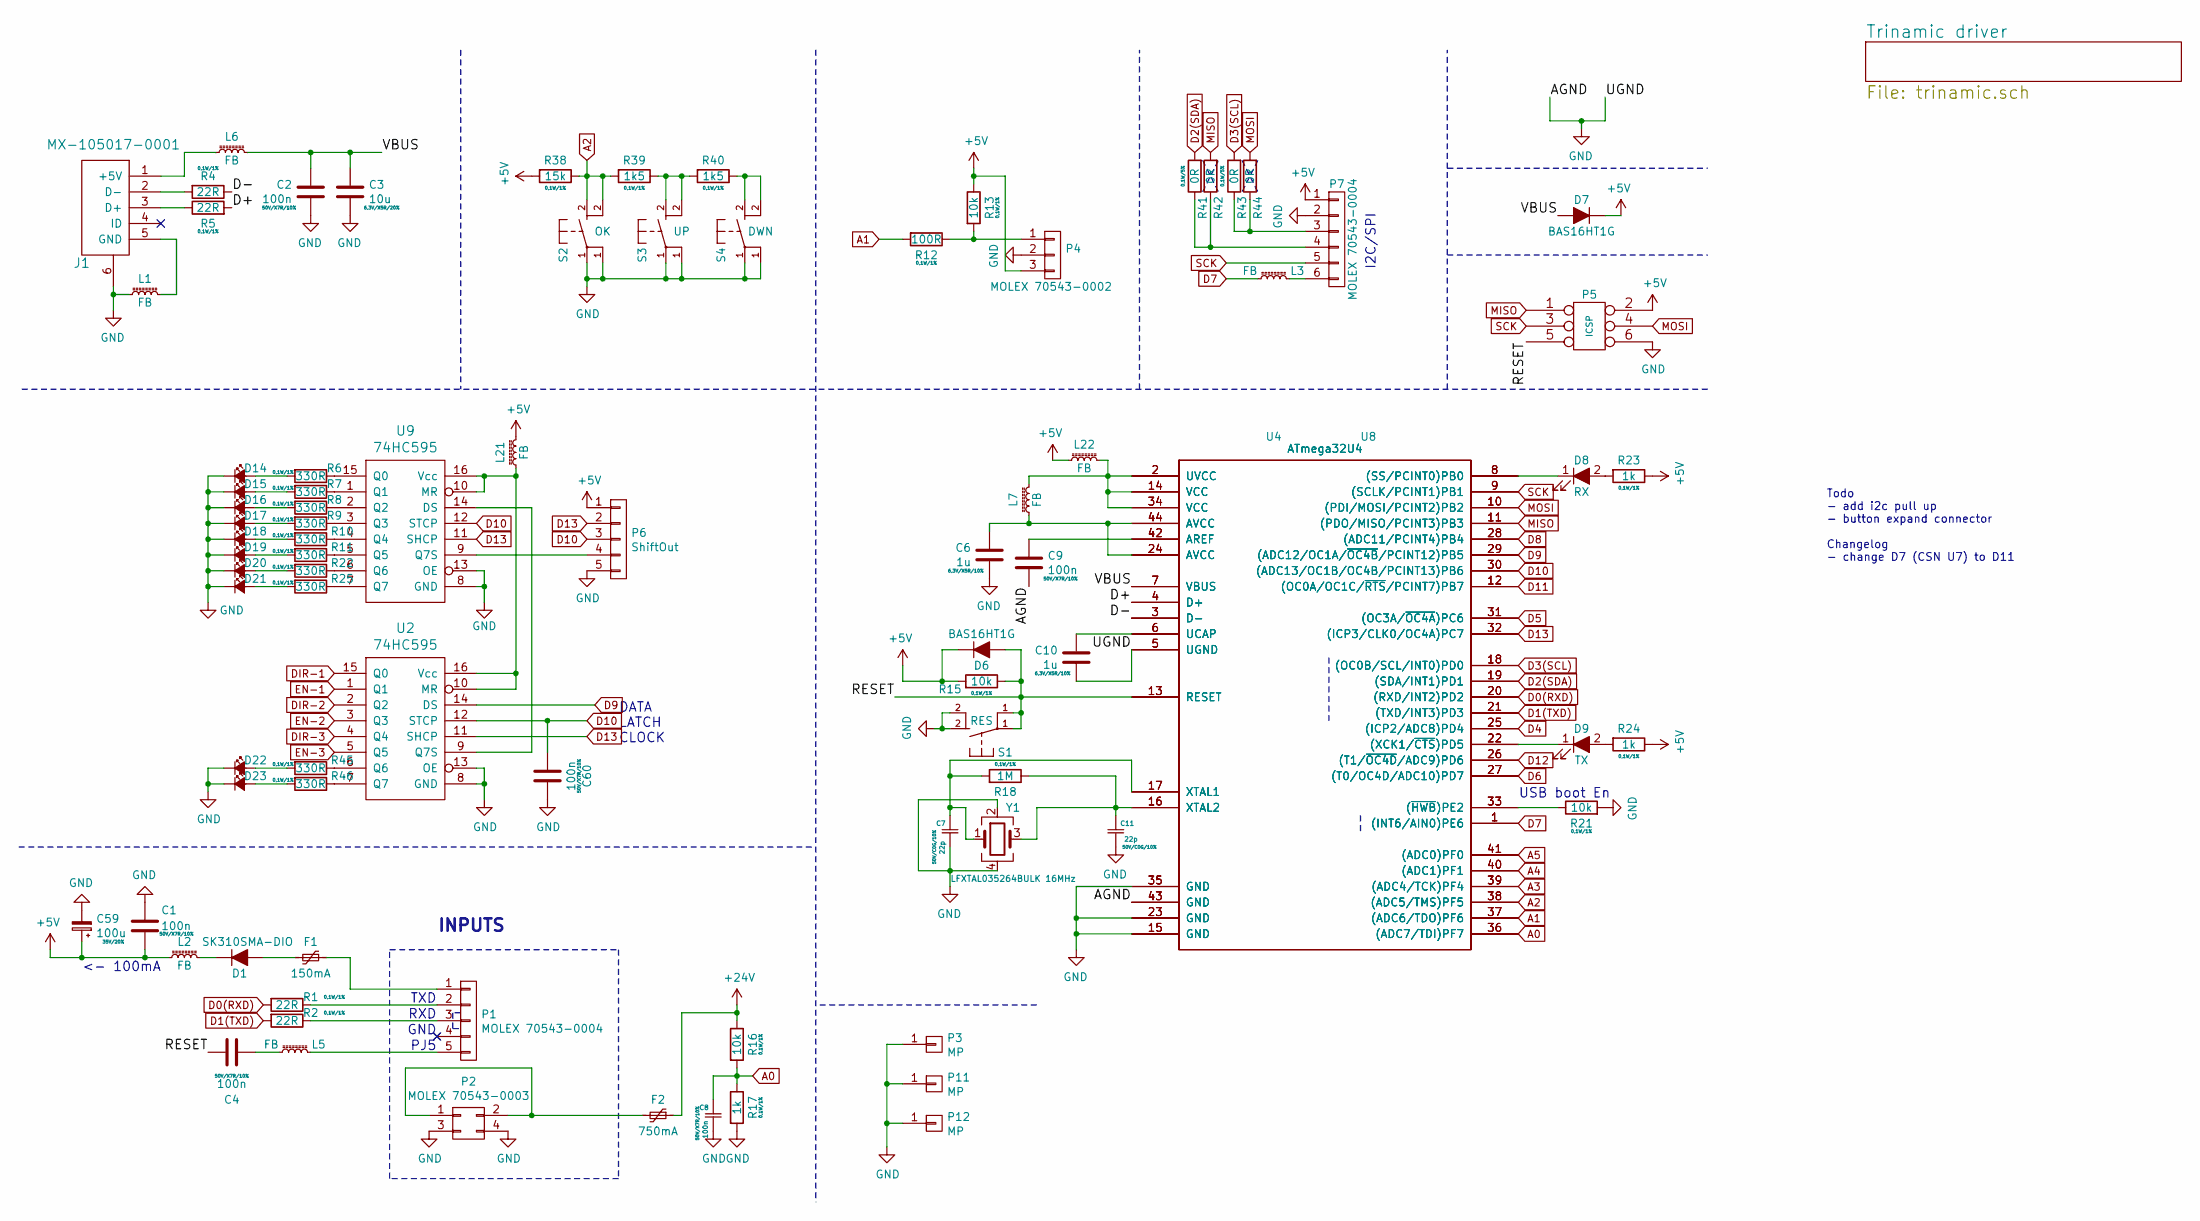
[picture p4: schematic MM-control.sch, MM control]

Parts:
C1, C2, C4, C8, C9, C60: 100n; C_0603
C3: 10u; C_0603
C6, C10: 1u; C_0603
C7, C11: 22p; C_0603
C59: 100u; c_elec_6.3x7.7
D1: SK310SMA-DIO; SMA_Standard
D6, D7: BAS16HT1G; SOD-323
D8: RX; LED_0805
D9: TX; LED_0805
D14, D16, D18, D20, D22: KPA-3010MGC; LED-1104
D15, D17, D19, D21, D23: KPA-3010SECK; LED-1104
F1: 150mA; R_1812
F2: 750mA; R_1812
J1: MX-105017-0001; USB-micro
L1, L2, L3, L5, L6, L7, L21, L22: FB; R_0603
P1: MOLEX 70543-0004; Pin_1x05-XL
P2: MOLEX 70543-0003; Pin_1x04-XL
P3, P11, P12: MP; MountingHole_3.2mm_M3_ISO14580_Pad
P4: MOLEX 70543-0002; Pin_1x03-XL
P5: ICSP; Pin_Header_Straight_2x03
P6: ShiftOut; Pin_1x05-XL
P7: MOLEX 70543-0004; Pin_1x06-XL
R1, R2, R4, R5: 22R; R_0603
R6, R7, R8, R9, R10, R11, R22, R25, R45, R46: 330R; R_0603
R12: 100R; R_0603
R13, R15, R16, R21: 10k; R_0603
R17, R23, R24: 1k; R_0603
R18: 1M; R_0603
R38: 15k; R_0603
R39, R40: 1k5; R_0603
R41, R42, R43, R44: 0R; R_0603
S1: RES; TACT-90
S2: OK; TACT-90
S3: UP; TACT-90
S4: DWN; TACT-90
U2, U9: 74HC595; SOIC-16_3.9x9.9mm_Pitch1.27mm
U4: ATmega32U4; TQFP-44_10x10mm_Pitch0.8mm
U8: ATmega32U4; QFN-44-1EP_7x7mm_Pitch0.5mm
Y1: LFXTAL035264BULK 16MHz; Crystal-3.2x2.5mm

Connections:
+5V: C1.1, C59.1, D6.1 (K), D7.1 (K), L2.1, L21.2, L22.1, P4.3, P5.2, P6.1, P7.1, R13.1, R15.2, R23.1, R24.1, R38.2; also elsewhere on the board
+24V: F2.1, R16.1; also elsewhere on the board
/D+: R5.2, U4.4 (D+), U8.4 (D+)
/D-: R4.1, U4.3 (D-), U8.3 (D-)
/RESET: C4.2, D6.2 (A), P5.5, R15.1, S1.1, U4.13 (RESET), U8.13 (RESET)
/VBUS: C2.2, C3.2, D7.2 (A), L6.2, U4.7 (VBUS), U8.7 (VBUS)
A0: C8.1, R16.2, R17.1, U4.36 ((ADC7/TDI)PF7), U8.36 ((ADC7/TDI)PF7)
A1: R12.2, U4.37 ((ADC6/TDO)PF6), U8.37 ((ADC6/TDO)PF6)
A2: R38.1, R39.2, S2.2, U4.38 ((ADC5/TMS)PF5), U8.38 ((ADC5/TMS)PF5)
A3: U4.39 ((ADC4/TCK)PF4), U8.39 ((ADC4/TCK)PF4); also elsewhere on the board
A4: U4.40 ((ADC1)PF1), U8.40 ((ADC1)PF1); also elsewhere on the board
A5: U4.41 ((ADC0)PF0), U8.41 ((ADC0)PF0); also elsewhere on the board
D0(RXD): R1.2, U4.20 ((RXD/INT2)PD2), U8.20 ((RXD/INT2)PD2)
D1(TXD): R2.2, U4.21 ((TXD/INT3)PD3), U8.21 ((TXD/INT3)PD3)
D2(SDA): R41.2, U4.19 ((SDA/INT1)PD1), U8.19 ((SDA/INT1)PD1)
D3(SCL): R43.2, U4.18 ((OC0B/SCL/INT0)PD0), U8.18 ((OC0B/SCL/INT0)PD0)
D4: U4.25 ((ICP2/ADC8)PD4), U8.25 ((ICP2/ADC8)PD4); also elsewhere on the board
D5: U4.31 ((OC3A/~OC4A~)PC6), U8.31 ((OC3A/~OC4A~)PC6); also elsewhere on the board
D6: U4.27 ((T0/OC4D/ADC10)PD7), U8.27 ((T0/OC4D/ADC10)PD7); also elsewhere on the board
D7: L3.1, U4.1 ((INT6/AIN0)PE6), U8.1 ((INT6/AIN0)PE6)
D8: U4.28 ((ADC11/PCINT4)PB4), U8.28 ((ADC11/PCINT4)PB4); also elsewhere on the board
D9: U2.14 (DS), U4.29 ((ADC12/OC1A/~OC4B~/PCINT12)PB5), U8.29 ((ADC12/OC1A/~OC4B~/PCINT12)PB5)
D10: C60.2, P6.3, U2.12 (STCP), U4.30 ((ADC13/OC1B/OC4B/PCINT13)PB6), U8.30 ((ADC13/OC1B/OC4B/PCINT13)PB6), U9.12 (STCP)
D11: U4.12 ((OC0A/OC1C/~RTS~/PCINT7)PB7), U8.12 ((OC0A/OC1C/~RTS~/PCINT7)PB7); also elsewhere on the board
D12: U4.26 ((T1/~OC4D~/ADC9)PD6), U8.26 ((T1/~OC4D~/ADC9)PD6); also elsewhere on the board
D13: P6.2, U2.11 (SHCP), U4.32 ((ICP3/CLK0/OC4A)PC7), U8.32 ((ICP3/CLK0/OC4A)PC7), U9.11 (SHCP)
DIR-1: U2.15 (Q0); also elsewhere on the board
DIR-2: U2.2 (Q2); also elsewhere on the board
DIR-3: U2.4 (Q4); also elsewhere on the board
EN-1: U2.1 (Q1); also elsewhere on the board
EN-2: U2.3 (Q3); also elsewhere on the board
EN-3: U2.5 (Q5); also elsewhere on the board
GND: C1.2, C2.1, C3.1, C6.1, C7.2, C8.2, C9.1, C10.1, C11.2, C59.2, C60.1, D14.1 (K), D15.1 (K), D16.1 (K), D17.1 (K), D18.1 (K), D19.1 (K), D20.1 (K), D21.1 (K), D22.1 (K), D23.1 (K), J1.6, L1.1, P2.3, P2.4, P3.1, P4.2, P5.6, P6.5, P7.2, P11.1, P12.1, R17.2, R21.2, S1.2, S2.1, S3.1, S4.1, U2.8 (GND), U2.13 (OE), U4.5 (UGND), U4.15 (GND), U4.23 (GND), U4.35 (GND), U4.43 (GND), U8.5 (UGND), U8.15 (GND), U8.23 (GND), U8.35 (GND), U8.43 (GND), U9.8 (GND), U9.13 (OE), Y1.2, Y1.4; also elsewhere on the board
MISO: P5.1, R42.2, U4.11 ((PDO/MISO/PCINT3)PB3), U8.11 ((PDO/MISO/PCINT3)PB3); also elsewhere on the board
MOSI: P5.4, R44.2, U4.10 ((PDI/MOSI/PCINT2)PB2), U8.10 ((PDI/MOSI/PCINT2)PB2); also elsewhere on the board
unnamed: C4.1, L5.1
unnamed: C6.2, L7.1, U4.24 (AVCC), U4.44 (AVCC), U8.24 (AVCC), U8.44 (AVCC)
unnamed: C7.1, R18.2, U4.17 (XTAL1), U8.17 (XTAL1), Y1.1
unnamed: C9.2, U4.42 (AREF), U8.42 (AREF)
unnamed: C10.2, U4.6 (UCAP), U8.6 (UCAP)
unnamed: C11.1, R18.1, U4.16 (XTAL2), U8.16 (XTAL2), Y1.3
unnamed: D1.1 (K), L2.2
unnamed: D1.2 (A), F1.2
unnamed: D8.1 (K), U4.8 ((SS/PCINT0)PB0), U8.8 ((SS/PCINT0)PB0)
unnamed: D8.2 (A), R23.2
unnamed: D9.1 (K), U4.22 ((XCK1/~CTS~)PD5), U8.22 ((XCK1/~CTS~)PD5)
unnamed: D9.2 (A), R24.2
unnamed: D14.2 (A), R6.2
unnamed: D15.2 (A), R7.2
unnamed: D16.2 (A), R8.2
unnamed: D17.2 (A), R9.2
unnamed: D18.2 (A), R10.2
unnamed: D19.2 (A), R11.2
unnamed: D20.2 (A), R22.2
unnamed: D21.2 (A), R25.2
unnamed: D22.2 (A), R45.2
unnamed: D23.2 (A), R46.2
unnamed: F1.1, P1.1
unnamed: F2.2, P2.1, P2.2
unnamed: J1.1 (+5V), L6.1
unnamed: J1.2 (D-), R4.2
unnamed: J1.3 (D+), R5.1
unnamed: J1.5 (GND), L1.2
unnamed: L3.2, P7.6
unnamed: L5.2, P1.5
unnamed: L21.1, U2.10 (MR), U2.16 (Vcc), U9.10 (MR), U9.16 (Vcc)
unnamed: L7.2, L22.2, U4.2 (UVCC), U4.14 (VCC), U4.34 (VCC), U8.2 (UVCC), U8.14 (VCC), U8.34 (VCC)
unnamed: P1.2, R1.1
unnamed: P1.3, R2.1
unnamed: P4.1, R12.1, R13.2
unnamed: P6.4, U9.9 (Q7S)
unnamed: P7.3, R43.1, R44.1
unnamed: P7.4, R41.1, R42.1
unnamed: R6.1, U9.15 (Q0)
unnamed: R7.1, U9.1 (Q1)
unnamed: R8.1, U9.2 (Q2)
unnamed: R9.1, U9.3 (Q3)
unnamed: R10.1, U9.4 (Q4)
unnamed: R11.1, U9.5 (Q5)
unnamed: R21.1, U4.33 ((~HWB~)PE2), U8.33 ((~HWB~)PE2)
unnamed: R22.1, U9.6 (Q6)
unnamed: R25.1, U9.7 (Q7)
unnamed: R39.1, R40.2, S3.2
unnamed: R40.1, S4.2
unnamed: R45.1, U2.6 (Q6)
unnamed: R46.1, U2.7 (Q7)
unnamed: U2.9 (Q7S), U9.14 (DS)
SCK: P5.3, P7.5, U4.9 ((SCLK/PCINT1)PB1), U8.9 ((SCLK/PCINT1)PB1); also elsewhere on the board

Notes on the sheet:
TXD
RXD
PJ5
USB boot En
INPUTS
DATA LATCH CLOCK
GND
I2C/SPI
<- 100mA
Todo - add i2c pull up - button expand connector Changelog - change D7 (CSN U7) to D11

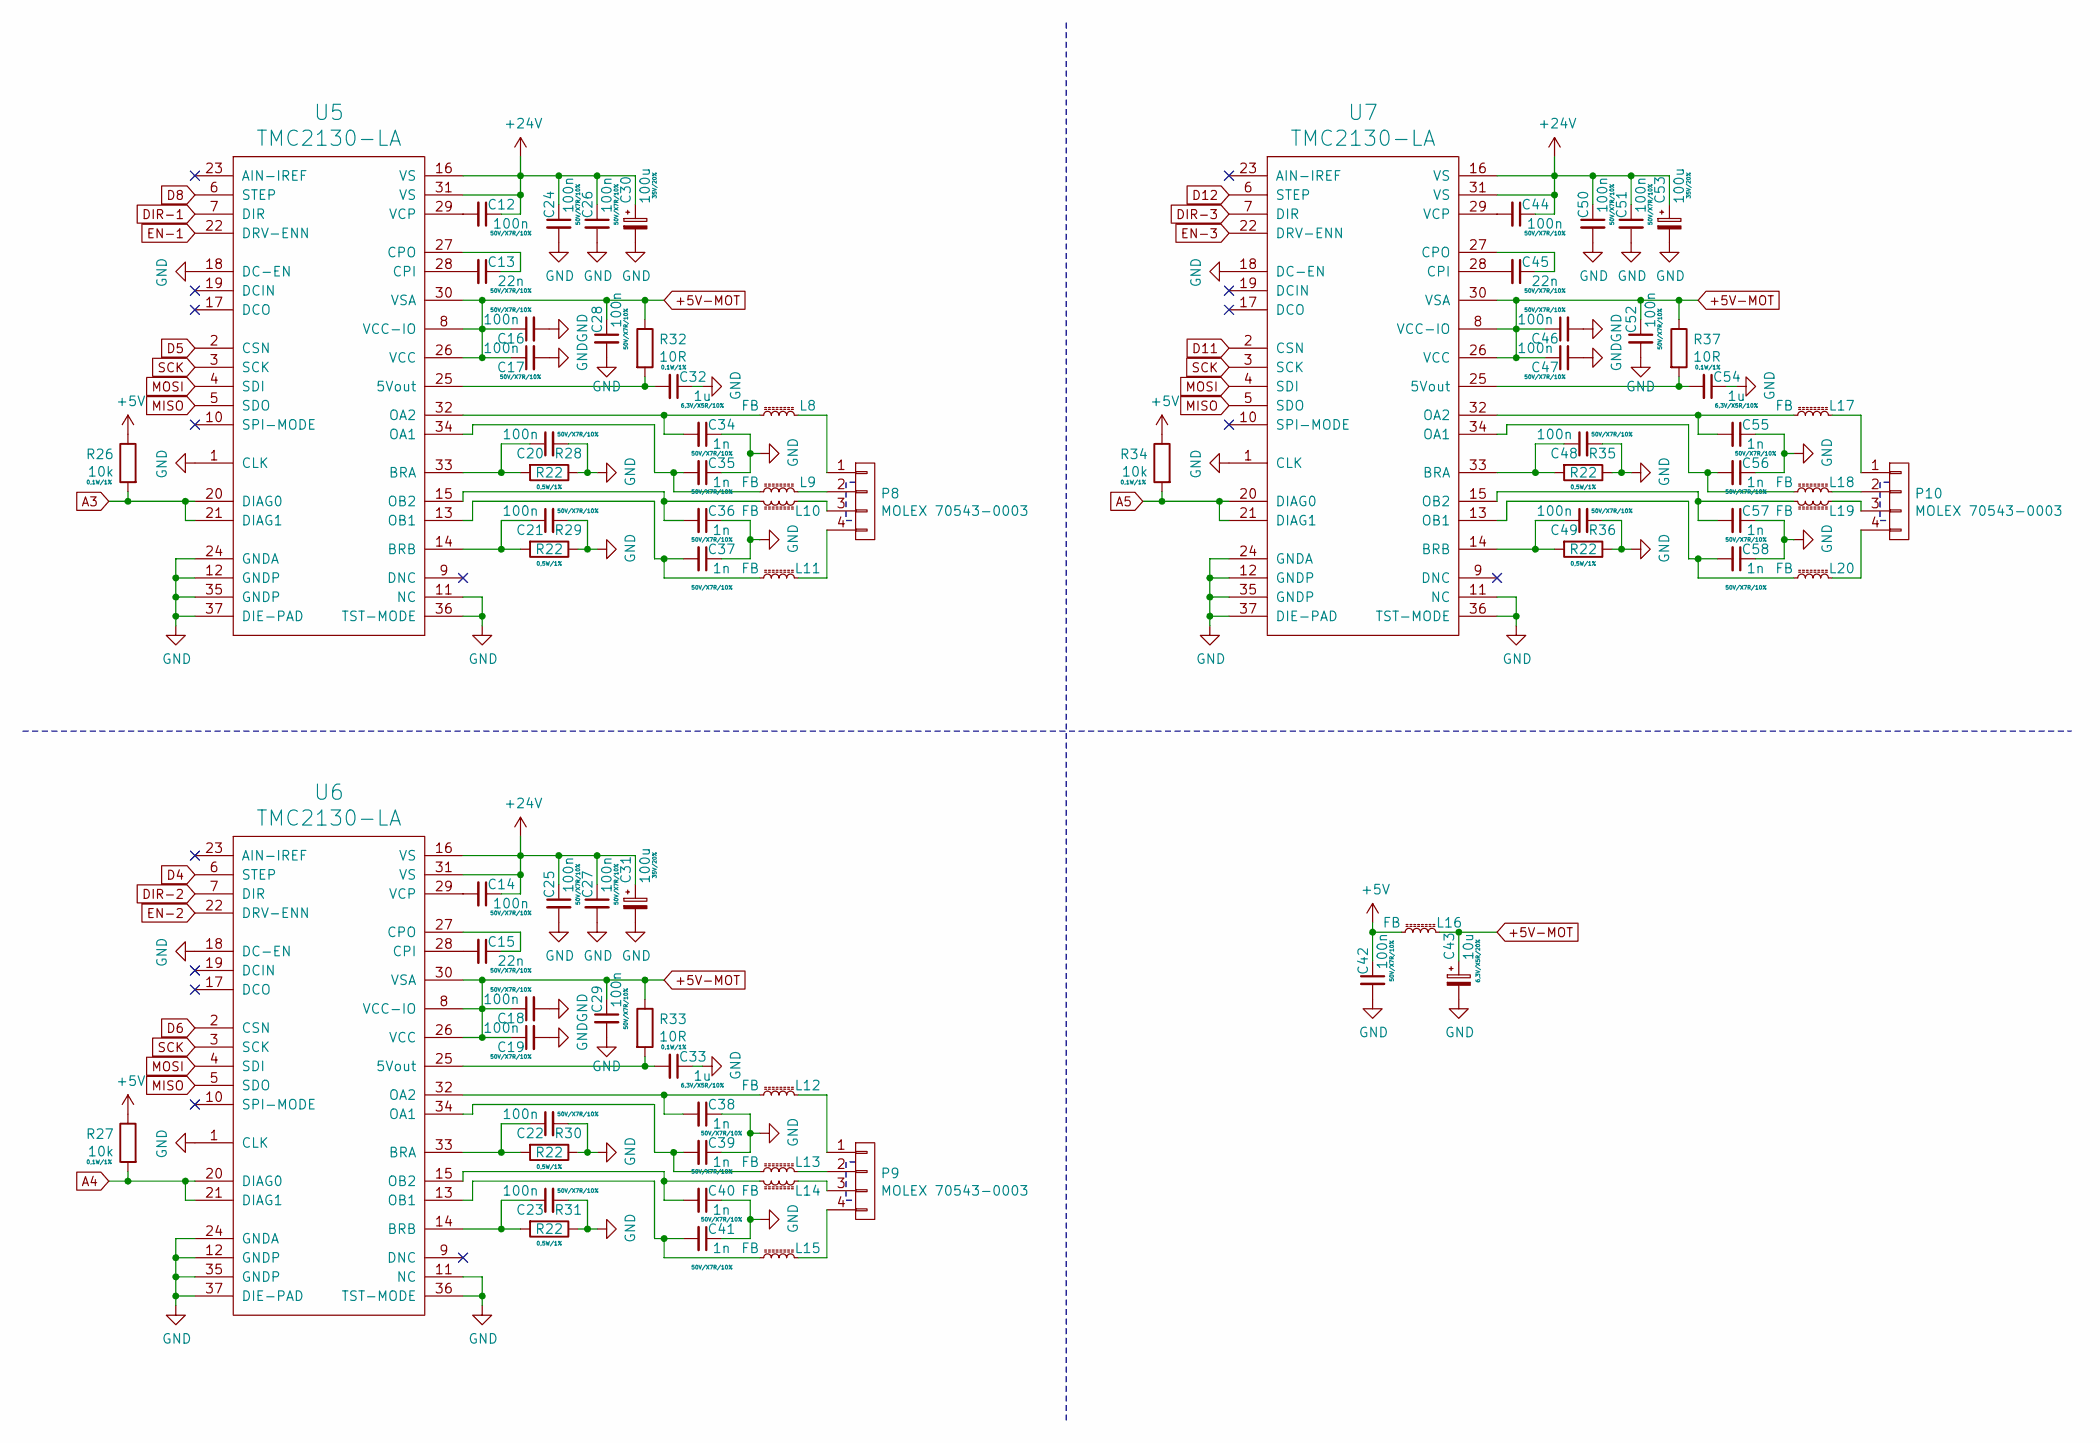
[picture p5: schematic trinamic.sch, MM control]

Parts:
C12, C14, C16, C17, C18, C19, C20, C21, C22, C23, C24, C25, C26, C27, C28, C29, C42, C44, C46, C47, C48, C49, C50, C51, C52: 100n; C_0603
C13, C15, C45: 22n; C_0603
C30, C31, C53: 100u; c_elec_6.3x7.7
C32, C33, C54: 1u; C_0603
C34, C35, C36, C37, C38, C39, C40, C41, C55, C56, C57, C58: 1n; C_0603
C43: 10u; C_0603
L8, L9, L10, L11, L12, L13, L14, L15, L16, L17, L18, L19, L20: FB; R_0603
P8, P9, P10: MOLEX 70543-0003; Pin_1x04-XL
R26, R27, R34: 10k; R_0603
R28, R29, R30, R31, R35, R36: R22; R_1206
R32, R33, R37: 10R; R_0603
U5, U6, U7: TMC2130-LA; QFN-36-1EP_5x6mm_Pitch0.5mm-GNDpad-0.3mm

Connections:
+5V: C42.1, L16.1, R26.1, R27.1, R34.1; also elsewhere on the board
+5V-MOT: C16.1, C17.1, C18.1, C19.1, C28.1, C29.1, C43.1, C46.1, C47.1, C52.1, L16.2, R32.1, R33.1, R37.1, U5.8 (VCC-IO), U5.26 (VCC), U5.30 (VSA), U6.8 (VCC-IO), U6.26 (VCC), U6.30 (VSA), U7.8 (VCC-IO), U7.26 (VCC), U7.30 (VSA)
+24V: C12.1, C14.1, C24.1, C25.1, C26.1, C27.1, C30.1, C31.1, C44.1, C50.1, C51.1, C53.1, U5.16 (VS), U5.31 (VS), U6.16 (VS), U6.31 (VS), U7.16 (VS), U7.31 (VS); also elsewhere on the board
A3: R26.2, U5.20 (DIAG0), U5.21 (DIAG1); also elsewhere on the board
A4: R27.2, U6.20 (DIAG0), U6.21 (DIAG1); also elsewhere on the board
A5: R34.2, U7.20 (DIAG0), U7.21 (DIAG1); also elsewhere on the board
D4: U6.6 (STEP); also elsewhere on the board
D5: U5.2 (CSN); also elsewhere on the board
D6: U6.2 (CSN); also elsewhere on the board
D8: U5.6 (STEP); also elsewhere on the board
D11: U7.2 (CSN); also elsewhere on the board
D12: U7.6 (STEP); also elsewhere on the board
DIR-1: U5.7 (DIR); also elsewhere on the board
DIR-2: U6.7 (DIR); also elsewhere on the board
DIR-3: U7.7 (DIR); also elsewhere on the board
EN-1: U5.22 (DRV-ENN); also elsewhere on the board
EN-2: U6.22 (DRV-ENN); also elsewhere on the board
EN-3: U7.22 (DRV-ENN); also elsewhere on the board
GND: C16.2, C17.2, C18.2, C19.2, C20.2, C21.2, C22.2, C23.2, C24.2, C25.2, C26.2, C27.2, C28.2, C29.2, C30.2, C31.2, C32.1, C33.1, C34.1, C35.1, C36.1, C37.1, C38.1, C39.1, C40.1, C41.1, C42.2, C43.2, C46.2, C47.2, C48.2, C49.2, C50.2, C51.2, C52.2, C53.2, C54.1, C55.1, C56.1, C57.1, C58.1, R28.1, R29.1, R30.1, R31.1, R35.1, R36.1, U5.1 (CLK), U5.11 (NC), U5.12 (GNDP), U5.18 (DC-EN), U5.24 (GNDA), U5.35 (GNDP), U5.36 (TST-MODE), U5.37 (DIE-PAD), U6.1 (CLK), U6.11 (NC), U6.12 (GNDP), U6.18 (DC-EN), U6.24 (GNDA), U6.35 (GNDP), U6.36 (TST-MODE), U6.37 (DIE-PAD), U7.1 (CLK), U7.11 (NC), U7.12 (GNDP), U7.18 (DC-EN), U7.24 (GNDA), U7.35 (GNDP), U7.36 (TST-MODE), U7.37 (DIE-PAD); also elsewhere on the board
MISO: U5.5 (SDO), U6.5 (SDO), U7.5 (SDO); also elsewhere on the board
MOSI: U5.4 (SDI), U6.4 (SDI), U7.4 (SDI); also elsewhere on the board
unnamed: C12.2, U5.29 (VCP)
unnamed: C13.1, U5.27 (CPO)
unnamed: C13.2, U5.28 (CPI)
unnamed: C14.2, U6.29 (VCP)
unnamed: C15.1, U6.27 (CPO)
unnamed: C15.2, U6.28 (CPI)
unnamed: C20.1, R28.2, U5.33 (BRA)
unnamed: C21.1, R29.2, U5.14 (BRB)
unnamed: C22.1, R30.2, U6.33 (BRA)
unnamed: C23.1, R31.2, U6.14 (BRB)
unnamed: C32.2, R32.2, U5.25 (5Vout)
unnamed: C33.2, R33.2, U6.25 (5Vout)
unnamed: C34.2, L8.1, U5.32 (OA2)
unnamed: C35.2, L9.1, U5.34 (OA1)
unnamed: C36.2, L10.1, U5.15 (OB2)
unnamed: C37.2, L11.1, U5.13 (OB1)
unnamed: C38.2, L12.1, U6.32 (OA2)
unnamed: C39.2, L13.1, U6.34 (OA1)
unnamed: C40.2, L14.1, U6.15 (OB2)
unnamed: C41.2, L15.1, U6.13 (OB1)
unnamed: C44.2, U7.29 (VCP)
unnamed: C45.1, U7.27 (CPO)
unnamed: C45.2, U7.28 (CPI)
unnamed: C48.1, R35.2, U7.33 (BRA)
unnamed: C49.1, R36.2, U7.14 (BRB)
unnamed: C54.2, R37.2, U7.25 (5Vout)
unnamed: C55.2, L17.1, U7.32 (OA2)
unnamed: C56.2, L18.1, U7.34 (OA1)
unnamed: C57.2, L19.1, U7.15 (OB2)
unnamed: C58.2, L20.1, U7.13 (OB1)
unnamed: L8.2, P8.1
unnamed: L9.2, P8.2
unnamed: L10.2, P8.3
unnamed: L11.2, P8.4
unnamed: L12.2, P9.1
unnamed: L13.2, P9.2
unnamed: L14.2, P9.3
unnamed: L15.2, P9.4
unnamed: L17.2, P10.1
unnamed: L18.2, P10.2
unnamed: L19.2, P10.3
unnamed: L20.2, P10.4
SCK: U5.3 (SCK), U6.3 (SCK), U7.3 (SCK); also elsewhere on the board

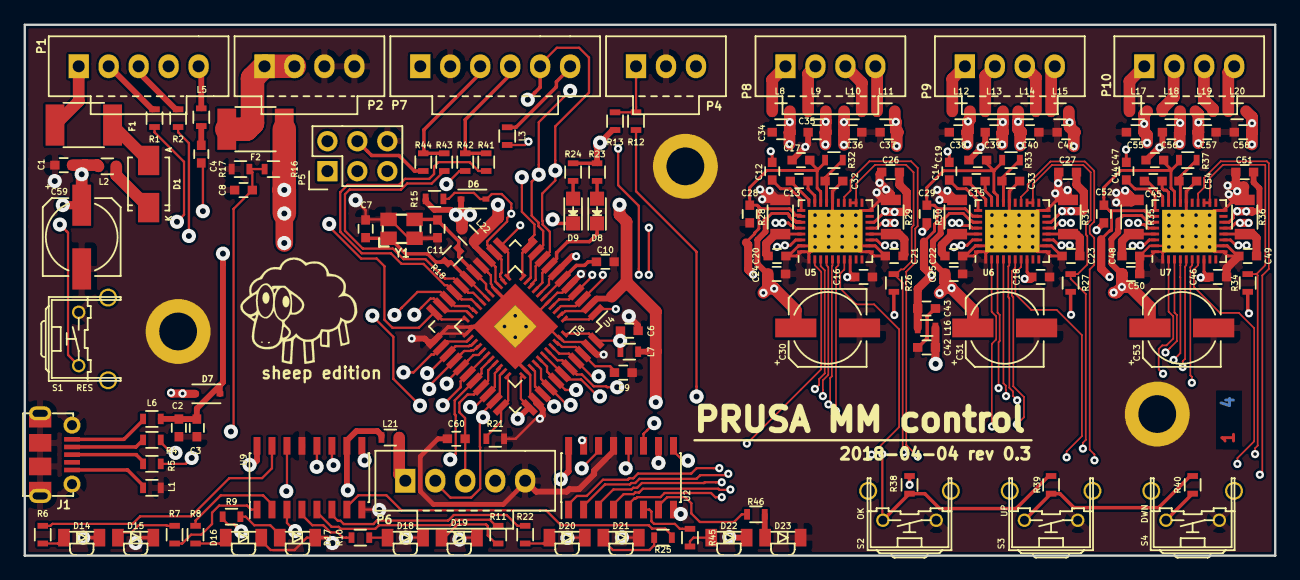
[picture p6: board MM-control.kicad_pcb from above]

Board: 4 copper layers, 106.0 x 45.0 mm, 164 parts (0 on the bottom side), 131 nets.
